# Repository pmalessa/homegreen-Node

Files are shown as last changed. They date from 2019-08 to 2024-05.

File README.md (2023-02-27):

# HomeGreen - self watering system
## Description
A self watering system for outdoor plants. This project contains the hardware and software files to completely build a HomeGreen node on your own.

The system is based on an inexpensive node, which is able to control up to 3 pumps and can be powered by nearly any conventional powerbank. It has a basic user interface using a 6-Digit 7-Segment Display combined with 4 touch buttons. As a pump, you could either use a 4-6V DC pump or a 5V relay to control a higher voltage pump. The node is designed to be water resistant and can be easily mounted using embedded magnets or a 3D printed holder.

## Repository structure
This repo contains everything you need to build a homegreen node on your own:

- hardware: The EAGLE PCB and GERBER files, BOM and models and dimensions for the case
- firmware: The firmware for the microcontroller (attiny88) on the node

## Hardware
The HomeGreen node PCB is designed to be enclosed in a 25mm diameter transparent pipe to be water resistant. The touch buttons can be used through the pipe without the need to open the case. The 2 ends need plastic caps, which could be easily 3D printed. one needs to be fully closed, while the other one needs to have an opening the for USB-A connector of the pump as well as the micro USB connector of the powerbank.

## Firmware
The firmware is written in low-level C++ and uses the PlatformIO framework. It is designed to run as energy efficient as possible to be able to run on a powerbank for a long time.

## Detailed description
The HomeGreen node contains the following main components:
- an attiny88 microcontroller as main controller
- a sophisticated power management circuit to be able to sleep and wake up the connected powerbank regularly
- a 6-Digit 7-Segment Display with its controller as user interface
- a 4-Channel touch button controller as user interface
- an I2C temperature sensor to measure the temperature of the environment
- a current limiter, step-up converter and a current measurement circuit to adjust and monitor the output power for the pump
- the ability to control up to 3 pumps sequentially using an additional HomeGreen Pump Hub

### Power management
The main issue of supplying your gadgets using a powerbank is the fact, that nearly all powerbanks shut off after a certain time of inactivity. As the sleep current draw of the HomeGreen node is substantially lower than any charge current the powerbank is designed for, it treats it as inactive and shuts off eventually. 

This led to the necessity to have a supercapacitor as an additional short-time energy storage onboard to be able to power the controller while in sleep and only wake the powerbank once the supercap is drained or it is time to enable the pump.

Additionally, each powerbank is behaving differently when it comes to the sleep and wake behavior. Some powerbanks wake up immediately once you connect the capacitive load of the supercap, while others require an additional substantial resistive load to enable its regulators. Strangely, some powerbanks even change their polarity and apply -2.5V to their output!

To support most of the available powerbanks on the market 2 MOSFETS back to back, combined with a charge pump and an additional controllable resistive load was necessary. Even with that, some powerbanks do not work reliably and should be avoided. A list of tested powerbanks will be added.

### User Interface
The HomeGreen Node consists of a 6-Digit 7-Segment display as well as 4 touch buttons to view its status and adjust all parameters to your needs. The HomeGreen Node can be used to control up to 3 pumps using an additional HomeGreen Pump Hub. Once connected, the user interface switches to the ability to adjust timing of each pump separately. However, if no Pump Hub is connected, it is simplyfied to control just one pump.

#### Sleep State
In its default sleep state, the 7-Segment Display is turned off and only the 2 Status LEDs are displaying its state. 
- If it blinks green once every 8 seconds, everything is fine. 
- If it blinks green twice and in a faster interval, it charges its supercap. This happens every 5-15mins. 
- If it blinks red, an error occured and the Node should be checked by waking it to get more details.
- If it is time to water the plants, it will wake itself and continue with the Pump State.
- To wake the Node, just touch one of its touch buttons. It will then try to wake the powerbank and will turn on its Display, once successful. It may take multiple tries sometimes depending on the model of powerbank. It then moves into Info State. If an error occured, it will switch into Error State after wake up before going to Info State.

#### Info State
In the info state, you see the set interval and duration of the pump cycle as well as the time left till the next pump cycle at one glance. If a Pump Hub is connected, you can switch between the config for each pump with a short press of the SET button.
- If no button is pressed, it shuts off and switches back to Sleep State after some time.
- To adjust the interval or duration of the pump cycle, long press the SET button and wait for the display to fade out and in. It now switched into Config State.
- To start a manual pump cycle, just long press the MANUAL button. It then switches into Pump State.

#### Config State
In the Config State, you can adjust the interval and duration of the pump cycle. The currently selected parameter is displayed by blinking its number.
- To increase the parameter, short press or hold the + button.
- To decrease the parameter, short press of hold the - button.
- To switch the selected parameter, short press the SET button.
- To save the newly configured parameters, long press the SET button. It switches to Info State then.
- If no button have been pressed for a longer period, changes are discarded and it switches to Info State.
- To get more advanced information and configuration options, long press the MANUAL button to switch to Advanced State.

#### Pump State
Once the pump interval elapsed or a manual pump cycle has been started, the Node switches into Pump State. In Pump State, an animation is displayed as well as the time left to pump in the current cycle. If a Pump Hub is connected, it will additionally display which pump is currently enabled.
- To increase the current pump cycle by 1 minute, short press the + button.
- To decrease the current pump cycle by 1 minute, short press the - button.
- To manually switch to the next pump, short press the SET button.
- To stop the current pump cycle, long press the MANUAL button.
- Once the pump duration of all pumps elapsed, the Node will switch to Info State to shortly display its current parameters, and after some time of inactivity it switches back to Sleep State.

#### Error State
If an error ocurred, the red led blinks to signal that something went wrong. To check for details, wake the node and it will switch to this state.
The following errors are possible:
- PB_ERR: Powerbank-Error - The node was not possible to wake the powerbank at its last wake up by a pump cycle or a user action. Check the charge state or cabling of the powerbank. Maybe that model is incompatible with the Node, check the list of tested powerbanks for hints.
- P1_ERR/P2_ERR/P3_ERR: Pump1/2/3-Error - There is an issue with the mentioned pump, the current draw had an anomaly. Maybe the cable is broken, the water tank is empty or the pump is clogged.
- EP_ERR: EEPROM-Error - There is an issue with the save state of the configuration. This rarely happens, but sometimes the config can get corrupted by battery drain. The config will be reset to default state and it has to be reconfigured.

The following interactions are possible:
- To clear the current error, short press any button.
- To ignore the current error permanently (until the next reset to defaults), long press the MANUAL button.

#### Advanced State
The Advanced State contains additional information and configuration options to move through.
The following informations are displayed:
- The build date of the firmware
- The build version of the firmware
- The current runtime in hours
- The total runtime in hours

The following interactions are possible:
- To move to the next information, short press the SET button
- To leave the Advanced State back to Info State, long press the SET button
- To reset all configurations to its default state, long press the MANUAL button. It then switches back to Info State.

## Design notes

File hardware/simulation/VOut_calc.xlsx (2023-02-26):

R1 [Ohm] | 91000.00
R2 [Ohm] | 10000.00
R3 [Ohm] | 100000.00
R4 [Ohm] | 100000.00
C1 [F]
VREF [V] | 0.60
V_PWM_H [V] | 3.30
V_PWM_L [V] | 0.00
VOUT_CONST | 6.06
Duty Cycle [%] | 0 | 10 | 20 | 30 | 40 | 50 | 60 | 70 | 80 | 90 | 100
PWM Voltage | 0.00 | 0.33 | 0.66 | 0.99 | 1.32 | 1.65 | 1.98 | 2.31 | 2.64 | 2.97 | 3.30
VOUT | 6.33 | 6.18 | 6.03 | 5.88 | 5.73 | 5.58 | 5.43 | 5.28 | 5.13 | 4.98 | 4.83

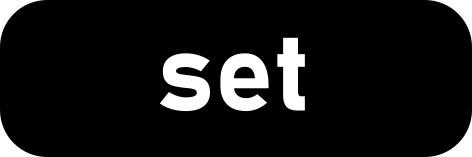
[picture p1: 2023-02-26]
design_files/bitmaps/button_set.png

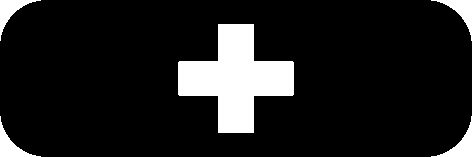
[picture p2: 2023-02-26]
design_files/bitmaps/button_plus.bmp

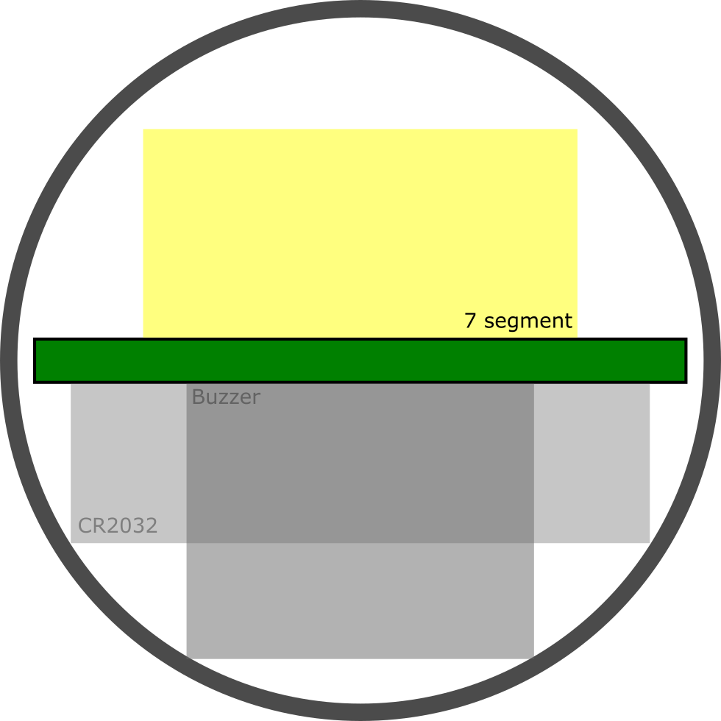
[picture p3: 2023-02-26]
design_files/svgs/Pipe.png

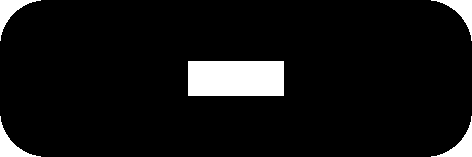
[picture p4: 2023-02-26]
design_files/bitmaps/button_minus.bmp

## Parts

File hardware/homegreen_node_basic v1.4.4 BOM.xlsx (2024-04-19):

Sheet: Sheet1
Qty | Value | Device | Package | Parts | Description
1 |  | ATTINY88 | TQFP32-08 | IC1
1 | 61400416021 | 61400416021 | 61400416021 | X3.1 | WR-COM USB 2.0 Type A Horizontal
1 | 0.33F | SUPERCAP | C_FYD0H104ZF | C3.1
10 | 100k | R-EU_R0805 | R0805 | R5.1, R5.2, R5.3, R5.4, R5.5, R5.6, R5.7, R5.8, R5.9, R5.10 | RESISTOR, European symbol
8 | 100n | C-EUC0805 | C0805 | C1.1, C1.2, C1.3, C1.4, C1.5, C1.6, C1.7, C1.8 | CAPACITOR, European symbol
3 | 10k | R-EU_R0805 | R0805 | R1.1, R1.2, R1.3 | RESISTOR, European symbol
4 | 10u | C-EUC0805 | C0805 | C2.1, C2.2, C2.3, C2.4 | CAPACITOR, European symbol
1 | 1M | R-EU_R0805 | R0805 | R6.1 | RESISTOR, European symbol
6 | 1k | R-EU_R0805 | R0805 | R2.1, R2.2, R2.3, R2.4, R2.5, R2.6 | RESISTOR, European symbol
1 | 20m | R-EU_R0805 | R0805 | R8.1 | RESISTOR, European symbol
1 | 330u | CPOL-EUD | PANASONIC_D | C4.1 | POLARIZED CAPACITOR, European symbol
2 | 3k | R-EU_R0805 | R0805 | R4.1, R4.2 | RESISTOR, European symbol
2 | 47 | R-EU_R0805 | R0805 | R3.1, R3.2 | RESISTOR, European symbol
3 | 4k7 | R-EU_R0805 | R0805 | R7.1, R7.2, R7.3 | RESISTOR, European symbol
4 | 5p | C-EUC0805 | C0805 | C5.1, C5.2, C5.3, C5.4 | CAPACITOR, European symbol
1 | 7-SEGMENT-6DIGIT-FJ3661BH | 7-SEGMENT-6DIGIT-FJ3661BH | 7SEG_6D_FJ3661BH | SEG1.1 | 2 Digit 7 Segment Display
3 | BAT54S | BAT54S | SOT23 | D1.1, D1.2, D1.3 | Schottky Diodes
2 | BC817DPN | BC817DPN | SOT23-6 | Q2.1, Q2.2
1 | DHT-4235A | SMD-BUTTON-TOP-DHT-4235A(4P-4.2X3.2MM) | SW4-SMD-4.2X3.2X2.5MM | SW1.1 | 311020045
1 | DSS24 | DIODE_SOD123 | SOD-123 | D2.1
1 | INA180 | INA180 | SOT23-5 | IC5.1
1 | JST-XH-06-PIN-ANGLED | JST-XH-06-PIN-ANGLED | JST-XH-06-PACKAGE-ROUND-PAD-ANGLED | X1.1 | JST XH Connector 2 Pin
1 | LM75B | LM75B | SO8 | IC2.1 | Digital temperature sensor and thermal watchdog
1 | MT3608 | MT3608 | SOT23-6 | IC8.1
1 | MT9700MT9700 | MT9700MT9700 | SOT23-5 | IC4.1
1 | TM1637-sop20 | DRIVER-TM1637(SOP20) | SOP20-1.27-12.7X7.65MM | IC6.1 | 310040027
1 | TTP224NS | TTP224NS | SSOP16 | IC3.1
1 | TYA40202R2M-10 | WE-LQSH_4020_744050420047 | WE-LQSH_4020 | L1.1 | WE-LQSH SMD Semi-Shielded High Saturation Power Inductor
1 | WST2011 | CJL2623SOT23-6 | SOT23-6 | Q1.1
1 | ZX62-B-5PA | MICRO-USB-SMD(ZX62-B-5PA) | ZX62-B-5PA | X2.1 | 320010005
1 | green | LEDKA-3528ASYC | KA-3528ASYC | LED1.1 | LED
1 | red | LEDKA-3528ASYC | KA-3528ASYC | LED2.1 | LED
2 | white | LEDCHIPLED_0805 | CHIPLED_0805 | LED3.1, LED3.2 | LED

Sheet: BOM
Qty | Value | Device | Package | Side | LCSC MPN | MPN | Link | Parts | needed for 30 pcbs | in stock | order lcsc
1 |  | ATTINY88 | TQFP32-08 | top | C111451 | ATTINY88-AU | https://lcsc.com/product-detail/ATMEL-AVR_MICROCHIP_ATTINY88-AU_ATTINY88-AU_C111451.html | IC1 | 30
1 | 61400416021 | 61400416021 | 61400416021 | top | C42643 | C42643 | https://lcsc.com/product-detail/USB-Connectors_Jing-Extension-of-the-Electronic-Co-C42643_C42643.html | X3.1 | 30
1 | 0.33F | SUPERCAP | C_FYD0H104ZF | bot | - |  |  | C3.1 | 30
10 | 100k | R-EU_R0805 | R0805 | 1xtop+9xbot | C96346 | RC0805FR-07100KL | https://lcsc.com/product-detail/Chip-Resistor-Surface-Mount_YAGEO-RC0805FR-07100KL_C96346.html | R5.1, R5.2, R5.3, R5.4, R5.5, R5.6, R5.7, R5.8, R5.9, R5.10 | 300
8 | 100n | C-EUC0805 | C0805 | bot | C49678 | CC0805KRX7R9BB104 | https://lcsc.com/product-detail/Multilayer-Ceramic-Capacitors-MLCC-SMD-SMT_YAGEO-CC0805KRX7R9BB104_C49678.html | C1.1, C1.2, C1.3, C1.4, C1.5, C1.6, C1.7, C1.8 | 240
3 | 10k | R-EU_R0805 | R0805 | bot |  |  |  | R1.1, R1.2, R1.3 | 90
4 | 10u | C-EUC0805 | C0805 | bot | C91245 | CL21A106MPFNNNE | https://lcsc.com/product-detail/Multilayer-Ceramic-Capacitors-MLCC-SMD-SMT_Samsung-Electro-Mechanics-CL21A106MPFNNNE_C91245.html | C2.1, C2.2, C2.3, C2.4 | 120
1 | 1M | R-EU_R0805 | R0805 | bot | C107699 | RC0805JR-071ML | https://lcsc.com/product-detail/Chip-Resistor-Surface-Mount_YAGEO-RC0805JR-071ML_C107699.html | R6.1 | 30
6 | 1k | R-EU_R0805 | R0805 | 2xtop+4xbot | C100046 | RC0805JR-071KL | https://lcsc.com/product-detail/Chip-Resistor-Surface-Mount_YAGEO-RC0805JR-071KL_C100046.html | R2.1, R2.2, R2.3, R2.4, R2.5, R2.6 | 180
1 | 20m | R-EU_R0805 | R0805 | 0 Ohm R? | C728492 | RL0805JR-070R02L | https://lcsc.com/product-detail/Chip-Resistor-Surface-Mount_YAGEO-RL0805JR-070R02L_C728492.html | R8.1 | 30 |  | 100
1 | 330u | CPOL-EUD | PANASONIC_D | bot | C128454 | EEEFTC331XAP | https://lcsc.com/product-detail/Aluminum-Electrolytic-Capacitors-SMD_PANASONIC-EEEFK0J331XP_C128454.html | C4.1 | 30
2 | 3k | R-EU_R0805 | R0805 | bot | C126350 | RC0805FR-073KL | https://lcsc.com/product-detail/Chip-Resistor-Surface-Mount_3KR-3001-1_C126350.html | R4.1, R4.2 | 60
2 | 47 | R-EU_R0805 | R0805 | 1xtop+1xbot | C107118 | CC0805JRNPO9BN470 | https://lcsc.com/product-detail/Multilayer-Ceramic-Capacitors-MLCC-SMD-SMT_YAGEO-CC0805JRNPO9BN470_C107118.html | R3.1, R3.2 | 60
3 | 4k7 | R-EU_R0805 | R0805 | bot | C60816 | RC0805FR-074K7L | https://lcsc.com/product-detail/Chip-Resistor-Surface-Mount_4-7K-4701-1_C60816.html | R7.1, R7.2, R7.3 | 90 |  | 200
4 | 5p | C-EUC0805 | C0805 | bot | C513573 | CL21C050CBANNNC | https://lcsc.com/product-detail/Multilayer-Ceramic-Capacitors-MLCC-SMD-SMT_YAGEO-CC0805DRNPO9BN5R0_C513573.html | C5.1, C5.2, C5.3, C5.4 | 120
1 | 7-SEGMENT-6DIGIT-FJ3661BH | 7-SEGMENT-6DIGIT-FJ3661BH | 7SEG_6D_FJ3661BH | top | C68298 | FJ3661BH | https://lcsc.com/product-detail/Led-Segment-Display_Shenzhen-Zhihao-Elec-FJ3661BH_C68298.html | SEG1.1 | 30
3 | BAT54S | BAT54S | SOT23 | top 9pcbs | C181201 | BAT54S | https://lcsc.com/product-detail/Schottky-Barrier-Diodes-SBD_Guangdong-Hottech-BAT54S_C181201.html | D1.1, D1.2, D1.3 | 90
2 | BC817DPN | BC817DPN | SOT23-6 | top 0 | C426778 | BC817DPN,115 | https://lcsc.com/product-detail/New-Arrivals_Nexperia-BC817DPN-115_C426778.html | Q2.1, Q2.2 | 60
1 | DHT-4235A | SMD-BUTTON-TOP-DHT-4235A(4P-4.2X3.2MM) | SW4-SMD-4.2X3.2X2.5MM | bot | C92589 | K2-1808SN-A4SW-01 | https://lcsc.com/product-detail/Tactile-Switches_Korean-Hroparts-Elec-K2-1808SN-A4SW-01_C92589.html | SW1.1 | 30
1 | DSS24 | DIODE_SOD123 | SOD-123 | top | C511865 | DSS24 | https://lcsc.com/product-detail/Schottky-Barrier-Diodes-SBD_BORN-DSS24_C511865.html | D2.1 | 30 |  | 40
1 | INA180A2 | INA180 | SOT23-5 | top | C192764 | INA180A2IDBVR | https://lcsc.com/product-detail/Operational-Amplifiers_Texas-Instruments-Texas-Instruments-INA180A2IDBVR_C192764.html | IC5.1 | 30 |  | 40
1 | JST-XH-06-PIN-ANGLED | JST-XH-06-PIN-ANGLED | JST-XH-06-PACKAGE-ROUND-PAD-ANGLED | bot | - | - | - | X1.1 | 30
1 | LM75B | LM75B | SO8 | bot | C34565 | LM75BD,118 | https://lcsc.com/product-detail/Temperature-Sensors_NXP-Semicon-LM75BD-118_C34565.html | IC2.1 | 30
1 | MT3608 | MT3608 | SOT23-6 | top | C84817 | MT3608 | https://lcsc.com/product-detail/DC-DC-Converters_XI-AN-Aerosemi-Tech-MT3608_C84817.html | IC8.1 | 30 |  | 50
1 | MT9700MT9700 | MT9700MT9700 | SOT23-5 | top | C89855 | MT9700 | https://lcsc.com/product-detail/PMIC-Power-Distribution-Switches_MT9700_C89855.html | IC4.1 | 30
1 | TM1637-sop20 | DRIVER-TM1637(SOP20) | SOP20-1.27-12.7X7.65MM | top | C265472 | TM1637 | https://lcsc.com/product-detail/LED-Drivers_GN-Semic-GN1637_C265472.html | IC6.1 | 30
1 | TTP224NS | TTP224NS | SSOP16 | top | C94149 | TTP224B-BSBN | https://lcsc.com/product-detail/Touch-Screen-Controller-ICs_Tontek-Design-Tech-TTP224B-BSBN_C94149.html | IC3.1 | 30
1 | TYA40202R2M-10 | WE-LQSH_4020_744050420047 | WE-LQSH_4020 | top 10 pcbs | C326299 | SNR4018K-2R2M | https://lcsc.com/product-detail/Power-Inductors_3L-COILS-SNR4018K-2R2M_C326299.html | L1.1 | 30 |  | 33
1 | WST2011 | CJL2623SOT23-6 | SOT23-6 | top | C148368 | WST2011 | https://lcsc.com/product-detail/MOSFET_Winsok-Semicon-WST2011_C148368.html | Q1.1 | 30
1 | ZX62-B-5PA | MICRO-USB-SMD(ZX62-B-5PA) | ZX62-B-5PA | bot | C10418 | C10418 | https://lcsc.com/product-detail/USB-Connectors_Jing-Extension-of-the-Electronic-Co-C10418_C10418.html | X2.1 | 30
1 | green | LEDKA-3528ASYC | KA-3528ASYC | top | C440443 | TJ-S3528UG6W9TLC2G-A5 | https://lcsc.com/product-detail/Light-Emitting-Diodes-LED_TOGIALED-TJ-S3528UG6W9TLC2G-A5_C440443.html | LED1.1 | 30
1 | red | LEDKA-3528ASYC | KA-3528ASYC | top | C74350 | 67-21/R6C-FN2Q1BZ/2T | https://lcsc.com/product-detail/Light-Emitting-Diodes-LED_Everlight-Elec-67-21-R6C-FN2Q1BZ-2T_C74350.html | LED2.1 | 30
2 | white | LEDCHIPLED_0805 | CHIPLED_0805 | top | C84258 | NCD0805W2 | https://lcsc.com/product-detail/Light-Emitting-Diodes-LED_Foshan-NationStar-Optoelectronics-NCD0805W2_C84258.html | LED3.1, LED3.2 | 60

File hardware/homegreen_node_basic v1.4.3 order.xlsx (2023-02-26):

Qty | Value | Device | Package | LCSC MPN | MPN | needed for 30 pcbs | in machine | in stock | order lcsc | order mouser | order reichelt | order ali
2 |  | 61400416021 | 61400416021 | C42643 | C42643 | 60 | - | 170
1 |  | ATTINY88 | TQFP32-08 | C111451 | ATTINY88-AU | 30 | - | 15 |  | 30
1 | 0.33F | SUPERCAP | C_FYD0H104ZF | - | - | 30 | - | 41
10 | 100k | R-EU_R0805 | R0805 | C96346 | RC0805FR-07100KL | 300 | 500
13 | 100n | C-EUC0805 | C0805 | C49678 | CC0805KRX7R9BB104 | 390 | 500
9 | 10u | C-EUC0805 | C0805 | C91245 | CL21A106MPFNNNE | 270 | 0 | 100 | 100
4 | 1M | R-EU_R0805 | R0805 | C107699 | RC0805JR-071ML | 120 | 500
14 | 1k | R-EU_R0805 | R0805 | C100046 | RC0805JR-071KL | 420 | 100 | 400
2 | 330u | CPOL-EUD | PANASONIC_D | C128454 | EEEFTC331XAP | 60 | - | 60
2 | 3k | R-EU_R0805 | R0805 | C126350 | RC0805FR-073KL | 60 | 150
3 | 47 | R-EU_R0805 | R0805 | C107118 | CC0805JRNPO9BN470 | 90 | 200
8 | 5p | C-EUC0805 | C0805 | C513573 | CL21C050CBANNNC | 240 | 200
4 | 6k8 | R-EU_R0805 | R0805 | C114550 | RC0805FR-076K8L | 120 | 200
2 | 7-SEGMENT-6DIGIT-FJ3661BH | 7-SEGMENT-6DIGIT-FJ3661BH | 7SEG_6D_FJ3661BH | C68298 | FJ3661BH | 60 | - | 6 | 35
2 | 74AHC1G66 | 74AHC1G66 | SOT65P212X110-5N | C96224 | 74AHC1G66GW,125 | 60 | 0 | 0 | 100
5 | BAT54S | BAT54S | SOT23 | C181201 | BAT54S | 150 | 200 |  | 0
4 | BC817DPN | BC817DPN | SOT23-6 | C426778 | BC817DPN,115 | 120 | 0 | 0 | 150
2 | WST2011 | CJL2623SOT23-6 | SOT23-6 | C148368 | WST2011 | 60 | 0 | 80 | 50
2 | DHT-4235A | SMD-BUTTON-TOP-DHT-4235A(4P-4.2X3.2MM) | SW4-SMD-4.2X3.2X2.5MM | C92589 | K2-1808SN-A4SW-01 | 60 | - | 24 | 100
1 | LM75B | LM75B | SO8 | C34565 | LM75BD,118 | 30 | 0 | 5 | 40
2 | MT9700MT9700 | MT9700MT9700 | SOT23-5 | C89855 | MT9700 | 60 | 0 | 35 | 100
2 | TM1637-sop20 | DRIVER-TM1637(SOP20) | SOP20-1.27-12.7X7.65MM | C265472 | TM1637 | 60 | - | 7 | 100
2 | TTP224NS | TTP224NS | SSOP16 | C94149 | TTP224B-BSBN | 60 | - | 8 |  |  |  | 100
2 | ZX62-B-5PA | MICRO-USB-SMD(ZX62-B-5PA) | ZX62-B-5PA | C10418 | C10418 | 60 | - | 100+ | 0
2 | green | LEDKA-3528ASYC | KA-3528ASYC | C440443 | TJ-S3528UG6W9TLC2G-A5 | 60 | 0 | 0 | 100
2 | red | LEDKA-3528ASYC | KA-3528ASYC | C74350 | 67-21/R6C-FN2Q1BZ/2T | 60 | 0 | 0 | 100
4 | white | LEDCHIPLED_0805 | CHIPLED_0805 | C84258 | NCD0805W2 | 120 | 0 | 0 | 200
1 | JST-XH-06-PIN-ROUND-PAD | JST-XH-06-PIN-ROUND-PAD | JST-XH-06-PACKAGE-ROUND-PAD | - | - | 30 | - |  |  |  | 50
1 |  | CONN_02JST-PTH-2 | JST-2-PTH | - |  | 5 | 0 | 0 |  |  | 10
1 |  | CONN_04JST-PTH | JST-4-PTH | - |  | 5 | 0 | 0 |  |  | 10
2 | 12p | C-EUC0805 | C0805 | C107108 | CC0805JRNPO9BN120 | 10 | 0 | 0 | 100
1 | 2k4 | R-EU_R0805 | R0805 | C114521 | RC0805FR-072K4L | 5 | 0 | 0 | 100
1 | 32.768kHz | CRYSTAL-32.768KHZSMD-3.2X1.5 | CRYSTAL-SMD-3.2X1.5MM | C48615 | Q13FC1350000200 | 5 | 0 | 0 | 10
2 | 74AHCT1G125 | 74AHCT1G125 | SOT353 | C12495 | 74AHCT1G125GW,125 | 10 | 0 | 0 | 20
1 | 7k5 | R-EU_R0805 | R0805 | C114547 | RC0805FR-077K5L | 5 | 0 | 0 | 100
1 | DMP3098 | PMOSSOT23 | SOT23-3 | C150492 | DMP3098L-7 | 5 | 0 | 0 | 20
2 | DSS24 | DIODE_SOD123 | SOD-123 | C466482 | DSS24 | 10 | 0 | 0 | 20
1 | DW06D | DW06D | SOT23-6 | C82123 | DW06D | 5 | 0 | 0 | 10
1 | ME6209A33M3G | ME6209SOT23-3 | SOT23-3 | C83508 | ME6209A33M3G | 5 | 0 | 0 | 10
1 | MT3608 | MT3608 | SOT23-6 | C84817 | MT3608 | 5 | 0 | 0 | 10
1 | TMP236 | TMP236 | SOT353 | C496107 | TMP236A4DCKR | 5 | 0 | 0 | 10
1 | TP4056 | TP4056 | ESOP-8 | C725790 | TP4056 | 5 | 0 | 0 | 10
1 | TYA40202R2M-10 | WE-LQSH_4020_744050420047 | WE-LQSH_4020 | C326299 | SNR4018K-2R2M | 5 | 0 | 0 | 10
1 | UBLOX_BMD_3XX | UBLOX_BMD_3XX | UBLOX_BMD_3XX | Mouser | BMD-360-A-R | 5 | 0 | 0 |  | 5

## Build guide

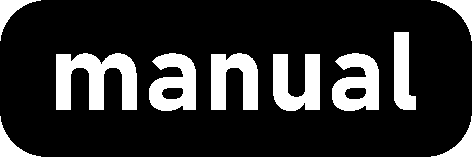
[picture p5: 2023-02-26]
design_files/bitmaps/button_manual.bmp

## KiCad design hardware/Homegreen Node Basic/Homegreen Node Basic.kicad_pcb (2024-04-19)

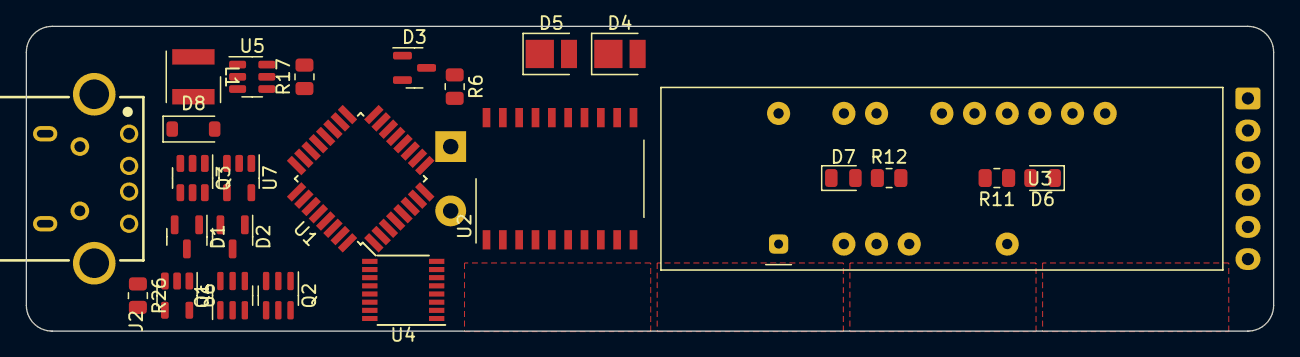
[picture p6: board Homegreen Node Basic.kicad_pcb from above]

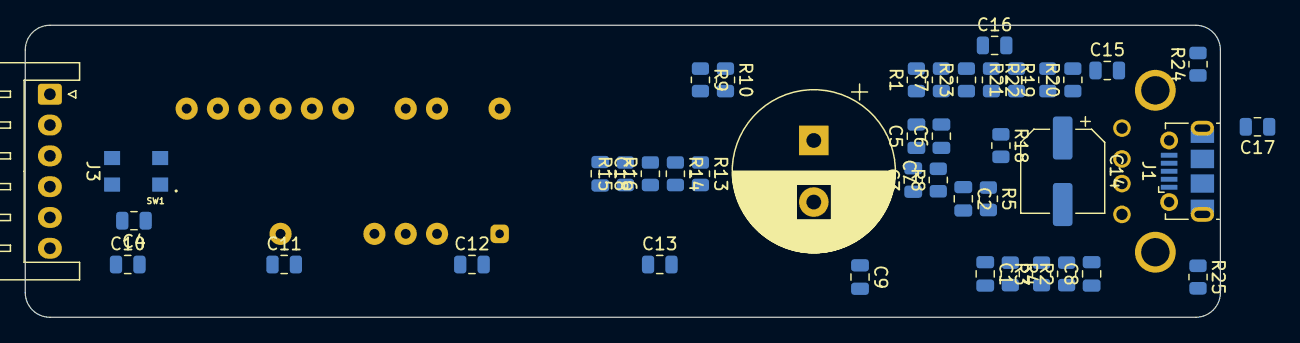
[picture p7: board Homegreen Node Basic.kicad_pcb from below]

Board: 2 copper layers, 97.0 x 23.7 mm, 67 parts (42 on the bottom side), 63 nets, no tracks yet.

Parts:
C1, C2, C3, C4, C5, C6, C8, C9, C18: 100n; C_0805_2012Metric
C7: 0.33F; CP_Radial_D13.0mm_P5.00mm
C10, C11, C12, C13: 5p; C_0805_2012Metric
C14: 330u; CP_Elec_6.3x5.8
C15, C16, C17: 10u; C_0805_2012Metric
D1, D2, D3: BAT54S; SOT-23
D4: gr; LED_PLCC_2835
D5: red; LED_PLCC_2835
D6, D7: wh; LED_0805_2012Metric
D8: DSS24; D_SOD-123
J1: USB_B_Micro; USB_Micro-B_Molex-105017-0001
J2: USB_A; Wuerth_61400416021
J3: Conn_01x06_Pin; JST_XH_S6B-XH-A_1x06_P2.50mm_Horizontal
L1: 2.2u; L_Wurth_WE-LQSH-4020
Q1, Q2: BC817DPN; SC-74-6_1.5x2.9mm_P0.95mm
Q3: WST2011; SOT-23-6
R1, R3, R7, R8, R15, R16, R17, R20, R24, R25: 100k; R_0805_2012Metric
R2, R6: 47; R_0805_2012Metric
R4, R11, R12, R13, R14, R21: 1k; R_0805_2012Metric
R5: 1M; R_0805_2012Metric
R9, R10: 3k; R_0805_2012Metric
R18: 4k7; R_0805_2012Metric
R19, R22, R23: 10k; R_0805_2012Metric
R26: 20m; R_0805_2012Metric
SW1: SW_Push; SW_DHT-4235A
U1: ATtiny88-A; TQFP-32_7x7mm_P0.8mm
U2: TM1637; SO-20_12.8x7.5mm_P1.27mm
U3: FJ3661BH
U4: TTP224; SSOP-16_3.9x4.9mm_P0.635mm
U5: MT3608; SOT-23-6
U6: INA180A2; SOT-23-5
U7: MT9700; SOT-23-5

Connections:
/BTN_LED: R11.2, R12.2, U1.8 (PB7)
/EN_CLK: C1.2, U1.13 (PB1)
/EN_LOAD: Q1.2 (B1), R4.2, U1.30 (PD0)
/EN_PUMP: R17.1, U1.22 (PA1), U5.4 (EN), U7.4 (EN)
/LED_ERR: R10.2, U1.11 (PD7)
/LED_OK: R9.2, U1.14 (PB2)
/MISO: J3.1, U1.16 (PB4)
/MOSI: J3.4, U1.15 (PB3)
/PUMP_CURRENT: U1.26 (PC3), U6.1
/PUMP_VOL: R23.1, U1.23 (PC0)
/RESET: C3.2, C4.1, J3.5, R8.1, SW1.1, U1.29 (~RESET/PC6)
/SCK: J3.3, U1.17 (PB5)
/TM_CLK: R13.2, R15.1, U1.10 (PD6)
/TM_DIO: R14.2, R16.1, U1.9 (PD5)
/TOUCH_PWR: C9.1, U1.3 (PA2), U4.6 (VDD), U4.11 (OD)
/USB1: J2.2 (D-), R24.1, U1.24 (PC1)
/USB2: J2.3 (D+), R25.1, U1.12 (PB0)
/User Interface/DIG1: U2.15 (GRID1), U3.22 (CA1)
/User Interface/DIG2: U2.14 (GRID2), U3.3 (CA2)
/User Interface/DIG3: U2.13 (GRID3), U3.4 (CA3)
/User Interface/DIG4: U2.12 (GRID4), U3.16 (CA4)
/User Interface/DIG5: U2.11 (GRID5), U3.13 (CA5)
/User Interface/DIG6: U2.10 (GRID6), U3.12 (CA6)
/User Interface/PAD_MANUAL: C13.1, U4.4 (TP3)
/User Interface/PAD_MINUS: C12.1, U4.3 (TP2)
/User Interface/PAD_PLUS: C10.1, U4.1 (TP0)
/User Interface/PAD_SET: C11.1, U4.2 (TP1)
/~EN_PB: D2.1 (A), U1.25 (PC2)
BAT_PWR: C3.1, C5.1, C6.1, C7.1, J3.2, R6.2, R8.2, U1.4 (VCC), U1.18 (AVCC)
GND: C2.2, C4.2, C5.2, C6.2, C7.2, C8.2, C9.2, C10.2, C11.2, C12.2, C13.2, C14.2, C15.2, C16.2, C17.2, C18.2, D4.1 (K), D5.1 (K), D6.1 (K), D7.1 (K), J1.5 (GND), J1.6 (Shield), J2.5 (Shield), J3.6, R2.2, R5.2, R7.1, R17.2, R18.2, R21.2, R24.2, R25.2, R26.2, SW1.2, U1.5 (GND), U1.21 (GND), U2.1 (GND), U4.5 (AHLB), U4.8 (LPMB), U4.10 (VSS), U5.2 (GND), U6.2 (GND), U6.4 (-), U7.2 (GND)
unnamed: C16.1, R22.1, R23.2
unnamed: D1.1 (A), Q2.1 (E1), R3.1
unnamed: D1.3 (COM), J1.1 (VBUS), Q3.6 (D)
unnamed: D1.2 (K), Q1.5 (B2), Q1.6 (C1)
unnamed: C1.1, D2.3 (COM)
unnamed: C2.1, D2.2 (K), Q3.1 (G), Q3.3 (G), R5.1
unnamed: D3.3 (COM), R6.1
unnamed: D4.2 (A), R9.1
unnamed: D5.2 (A), R10.1
unnamed: D6.2 (A), R11.1
unnamed: D7.2 (A), R12.1
unnamed: D8.2 (A), L1.2, U5.1 (SW)
unnamed: C14.1, C17.1, D8.1 (K), J2.1 (VBUS), R19.1, R20.1
unnamed: J2.4 (GND), R26.1, U6.3 (+)
unnamed: Q1.1 (E1), Q2.6 (C1), R2.1
unnamed: Q1.3 (C2), Q2.2 (B1), R3.2
unnamed: Q1.4 (E2), R4.1
unnamed: Q3.2 (S), Q3.5 (S)
unnamed: R1.1, R7.2, U1.19 (PA0)
unnamed: R13.1, U2.18 (CLK)
unnamed: R14.1, U2.17 (DIO)
unnamed: U2.2 (SEG1/KS1), U3.15 (A)
unnamed: U2.3 (SEG2/KS2), U3.20 (B)
unnamed: U2.4 (SEG3/KS3), U3.19 (C)
unnamed: U2.5 (SEG4/KS4), U3.5 (D)
unnamed: U2.6 (SEG5/KS5), U3.1 (E)
unnamed: U2.7 (SEG6/KS6), U3.14 (F)
unnamed: U2.8 (SEG7/KS7), U3.17 (G)
unnamed: U2.9 (SEG8/KS8), U3.8 (DP)
unnamed: R19.2, R20.2, R21.1, R22.2, U5.3 (FB)
unnamed: C15.1, L1.1, U5.5 (IN), U7.1 (VOUT)
unnamed: R18.1, U7.3 (SET)
USB_PWR: C8.1, C18.1, D3.1 (A), Q3.4 (D), R1.2, R15.2, R16.2, U2.16 (VDD), U6.5 (V+), U7.5 (VIN)

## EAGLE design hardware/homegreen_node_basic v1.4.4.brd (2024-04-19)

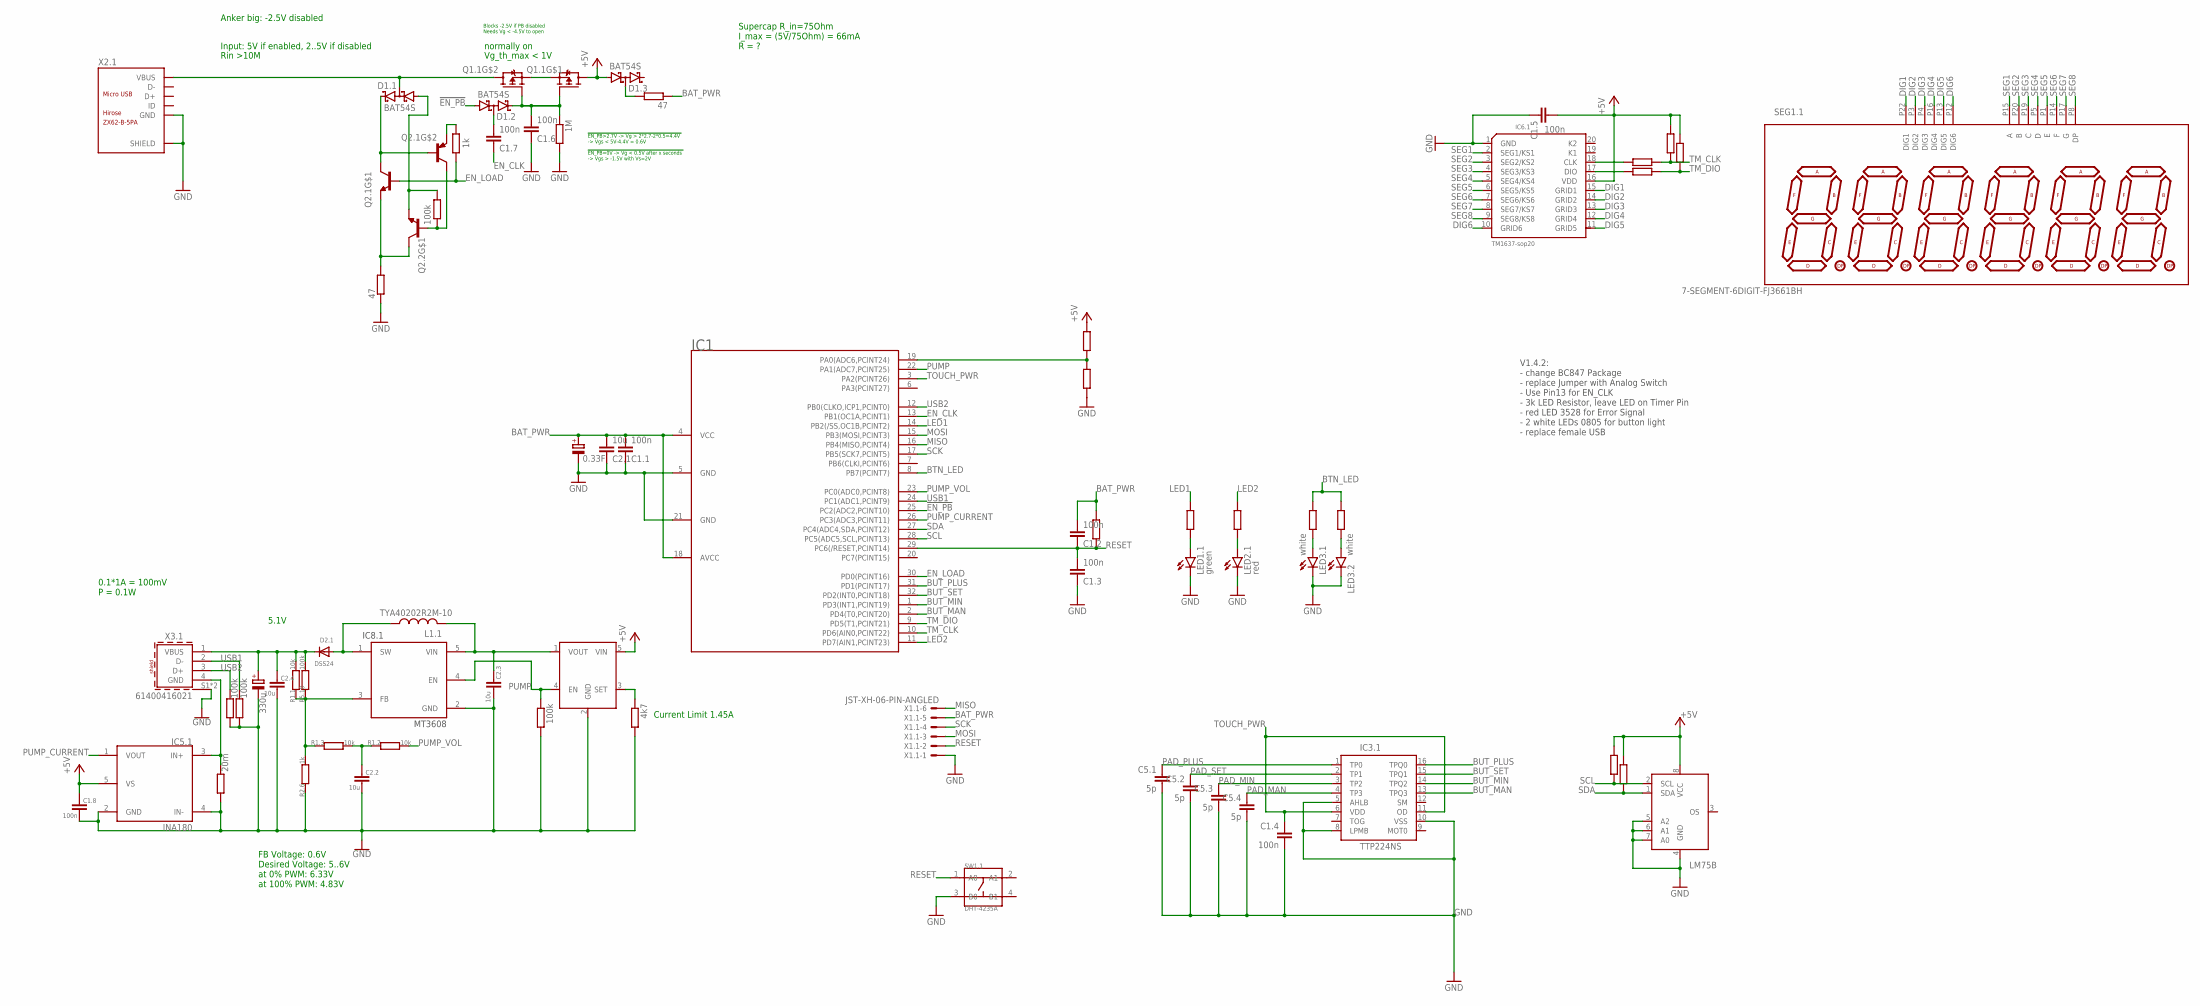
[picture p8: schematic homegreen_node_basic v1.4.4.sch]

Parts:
C1.1, C1.2, C1.3, C1.4, C1.5, C1.6, C1.7, C1.8: 100n; C0805
C2.1, C2.2, C2.3, C2.4: 10u; C0805
C3.1: 0.33F; C_FYD0H104ZF
C4.1: 330u; PANASONIC_D
C5.1, C5.2, C5.3, C5.4: 5p; C0805
D1.1, D1.2, D1.3: BAT54S; SOT23
D2.1: DSS24; SOD-123
IC1: ATTINY88; TQFP32-08
IC2.1: LM75B; SO8
IC3.1: TTP224NS; SSOP16
IC4.1: MT9700MT9700; SOT23-5
IC5.1: INA180; SOT23-5
IC6.1: TM1637-sop20; SOP20-1.27-12.7X7.65MM
IC8.1: MT3608; SOT23-6
L1.1: TYA40202R2M-10; WE-LQSH_4020
LED1.1: green; KA-3528ASYC
LED2.1: red; KA-3528ASYC
LED3.1, LED3.2: white; CHIPLED_0805
Q1.1: WST2011; SOT23-6
Q2.1, Q2.2: BC817DPN; SOT23-6
R1.1, R1.2, R1.3: 10k; R0805
R2.1, R2.2, R2.3, R2.4, R2.5, R2.6: 1k; R0805
R3.1, R3.2: 47; R0805
R4.1, R4.2: 3k; R0805
R5.1, R5.2, R5.3, R5.4, R5.5, R5.6, R5.7, R5.8, R5.9, R5.10: 100k; R0805
R6.1: 1M; R0805
R7.1, R7.2, R7.3: 4k7; R0805
R8.1: 20m; R0805
SEG1.1: 7-SEGMENT-6DIGIT-FJ3661BH; 7SEG_6D_FJ3661BH
SW1.1: DHT-4235A; SW4-SMD-4.2X3.2X2.5MM
X1.1: JST-XH-06-PIN-ANGLED; JST-XH-06-PACKAGE-ROUND-PAD-ANGLED
X2.1: ZX62-B-5PA
X3.1: 61400416021

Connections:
!EN_PB: D1.2.1 (A1), IC1.25 (PC2(ADC2,PCINT10))
+5V: C1.5.2, C1.8.1, D1.3.1 (A1), IC2.1.8 (VCC), IC4.1.5 (VIN), IC5.1.5 (VS), IC6.1.16 (VDD), Q1.1.6 (D), R5.3.1, R5.5.2, R5.6.2, R7.2.2, R7.3.2
BAT_PWR: C1.1.2, C1.2.2, C2.1.2, C3.1.+, IC1.4 (VCC), IC1.18 (AVCC), R3.2.1, R5.7.1, X1.1.5
BTN_LED: IC1.8 (PB7(PCINT7)), R2.1.2, R2.5.2
BUT_MAN: IC1.2 (PD4(T0,PCINT20)), IC3.1.13 (TPQ3)
BUT_MIN: IC1.1 (PD3(INT1,PCINT19)), IC3.1.14 (TPQ2)
BUT_PLUS: IC1.31 (PD1(PCINT17)), IC3.1.16 (TPQ0)
BUT_SET: IC1.32 (PD2(INT0,PCINT18)), IC3.1.15 (TPQ1)
DIG1: IC6.1.15 (GRID1), SEG1.1.P22 (DIG1)
DIG2: IC6.1.14 (GRID2), SEG1.1.P3 (DIG2)
DIG3: IC6.1.13 (GRID3), SEG1.1.P4 (DIG3)
DIG4: IC6.1.12 (GRID4), SEG1.1.P16 (DIG4)
DIG5: IC6.1.11 (GRID5), SEG1.1.P13 (DIG5)
DIG6: IC6.1.10 (GRID6), SEG1.1.P12 (DIG6)
EN_CLK: C1.7.1, IC1.13 (PB1(OC1A,PCINT1))
EN_LOAD: IC1.30 (PD0(PCINT16)), Q2.1.2 (B), R2.4.1
GND: C1.1.1, C1.3.1, C1.4.2, C1.5.1, C1.6.1, C1.8.2, C2.1.1, C2.2.2, C2.3.2, C2.4.2, C3.1.-, C4.1.-, C5.1.2, C5.2.2, C5.3.2, C5.4.2, IC1.5 (GND), IC1.21 (GND), IC2.1.4 (GND), IC2.1.5 (A2), IC2.1.6 (A1), IC2.1.7 (A0), IC3.1.5 (AHLB), IC3.1.8 (LPMB), IC3.1.10 (VSS), IC4.1.2 (GND), IC5.1.2 (GND), IC5.1.4 (IN-), IC6.1.1 (GND), IC8.1.2 (GND), LED1.1.C, LED2.1.C, LED3.1.C, LED3.2.C, R2.6.1, R3.1.1, R5.2.2, R5.4.2, R5.8.2, R5.9.2, R6.1.2, R7.1.2, R8.1.2, SW1.1.3 (B0), X1.1.1, X2.1.5 (GND), X2.1.P1 (SHIELD), X2.1.P2 (SHIELD), X2.1.P3 (SHIELD), X2.1.P4 (SHIELD), X2.1.P5 (SHIELD), X2.1.P6 (SHIELD), X3.1.S1 (SHIELD), X3.1.S2 (SHIELD)
LED1: IC1.14 (PB2(/SS,OC1B,PCINT2)), R4.1.2
LED2: IC1.11 (PD7(AIN1,PCINT23)), R4.2.2
MISO: IC1.16 (PB4(MISO,PCINT4)), X1.1.6
MOSI: IC1.15 (PB3(MOSI,PCINT3)), X1.1.3
unnamed: IC6.1.18 (CLK), R2.2.2
unnamed: C2.3.1, IC4.1.1 (VOUT), IC8.1.5 (VIN), L1.1.1
unnamed: Q1.1.2 (S), Q1.1.5 (S)
unnamed: IC6.1.17 (DIO), R2.3.2
unnamed: D1.3.3 (C1A2), R3.2.2
unnamed: Q2.1.1 (E), Q2.2.6 (C), R3.1.2
unnamed: LED1.1.A, R4.1.1
unnamed: IC1.19 (PA0(ADC6,PCINT24)), R5.3.2, R5.4.1
unnamed: C1.7.2, D1.2.3 (C1A2)
unnamed: Q2.1.4 (E), R2.4.2
unnamed: LED2.1.A, R4.2.1
unnamed: D1.1.2 (C2), Q2.1.5 (B), Q2.1.6 (C)
unnamed: C2.2.1, R1.2.1, R1.3.2
unnamed: D1.1.1 (A1), Q2.2.1 (E), R5.1.1
unnamed: Q2.1.3 (C), Q2.2.2 (B), R5.1.2
unnamed: LED3.1.A, R2.1.1
unnamed: C1.6.2, D1.2.2 (C2), Q1.1.1 (G), Q1.1.3 (G), R6.1.1
unnamed: LED3.2.A, R2.5.1
unnamed: C2.4.1, C4.1.+, D2.1.C, R1.1.2, R5.10.2, X3.1.1 (VBUS)
unnamed: IC5.1.3 (IN+), R8.1.1, X3.1.4 (GND)
unnamed: IC4.1.3 (SET), R7.1.1
unnamed: D2.1.A, IC8.1.1 (SW), L1.1.2
unnamed: IC8.1.3 (FB), R1.1.1, R1.3.1, R2.6.2, R5.10.1
PAD_MAN: C5.4.1, IC3.1.4 (TP3)
PAD_MIN: C5.3.1, IC3.1.3 (TP2)
PAD_PLUS: C5.1.1, IC3.1.1 (TP0)
PAD_SET: C5.2.1, IC3.1.2 (TP1)
PUMP: IC1.22 (PA1(ADC7,PCINT25)), IC4.1.4 (EN), IC8.1.4 (EN), R5.2.1
PUMP_CURRENT: IC1.26 (PC3(ADC3,PCINT11)), IC5.1.1 (VOUT)
PUMP_VOL: IC1.23 (PC0(ADC0,PCINT8)), R1.2.2
RESET: C1.2.1, C1.3.2, IC1.29 (PC6(/RESET,PCINT14)), R5.7.2, SW1.1.1 (A0), X1.1.2
SCK: IC1.17 (PB5(SCK7,PCINT5)), X1.1.4
SCL: IC1.28 (PC5(ADC5,SCL,PCINT13)), IC2.1.2 (SCL), R7.3.1
SDA: IC1.27 (PC4(ADC4,SDA,PCINT12)), IC2.1.1 (SDA), R7.2.1
SEG1: IC6.1.2 (SEG1/KS1), SEG1.1.P15 (A)
SEG2: IC6.1.3 (SEG2/KS2), SEG1.1.P20 (B)
SEG3: IC6.1.4 (SEG3/KS3), SEG1.1.P19 (C)
SEG4: IC6.1.5 (SEG4/KS4), SEG1.1.P5 (D)
SEG5: IC6.1.6 (SEG5/KS5), SEG1.1.P1 (E)
SEG6: IC6.1.7 (SEG6/KS6), SEG1.1.P14 (F)
SEG7: IC6.1.8 (SEG7/KS7), SEG1.1.P17 (G)
SEG8: IC6.1.9 (SEG8/KS8), SEG1.1.P8 (DP)
TM_CLK: IC1.10 (PD6(AIN0,PCINT22)), R2.2.1, R5.5.1
TM_DIO: IC1.9 (PD5(T1,PCINT21)), R2.3.1, R5.6.1
TOUCH_PWR: C1.4.1, IC1.3 (PA2(PCINT26)), IC3.1.6 (VDD), IC3.1.11 (OD)
USB1: IC1.24 (PC1(ADC1,PCINT9)), R5.9.1, X3.1.2 (D-)
USB2: IC1.12 (PB0(CLKO,ICP1,PCINT0)), R5.8.1, X3.1.3 (D+)
VBUS: D1.1.3 (C1A2), Q1.1.4 (D), X2.1.1 (VBUS)

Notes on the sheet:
V1.4.2: - change BC847 Package - replace Jumper with Analog Switch - Use Pin13 for EN_CLK - 3k LED Resistor, leave LED on Timer Pin - red LED 3528 for Error Signal - 2 white LEDs 0805 for button light - replace female USB
normally on
Input: 5V if enabled, 2..5V if disabled
Vg_th_max < 1V
Supercap R_in=75Ohm I_max = (5V/75Ohm) = 66mA R = ?
Rin >10M
!EN_PB>2.7V -> Vg > 2*2.7-2*0.5=4.4V -> Vgs < 5V-4.4V = 0.6V !EN_PB=0V -> Vg < 0.5V after x seconds -> Vgs > -1.5V with Vs=2V
Anker big: -2.5V disabled
Blocks -2.5V if PB disabled Needs Vg < -4.5V to open
5.1V
Current Limit 1.45A
FB Voltage: 0.6V Desired Voltage: 5..6V at 0% PWM: 6.33V at 100% PWM: 4.83V
0.1*1A = 100mV P = 0.1W

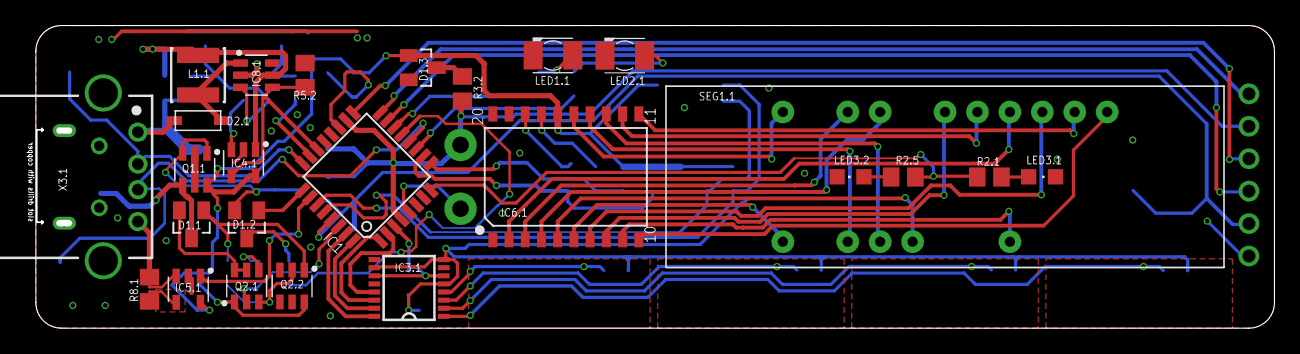
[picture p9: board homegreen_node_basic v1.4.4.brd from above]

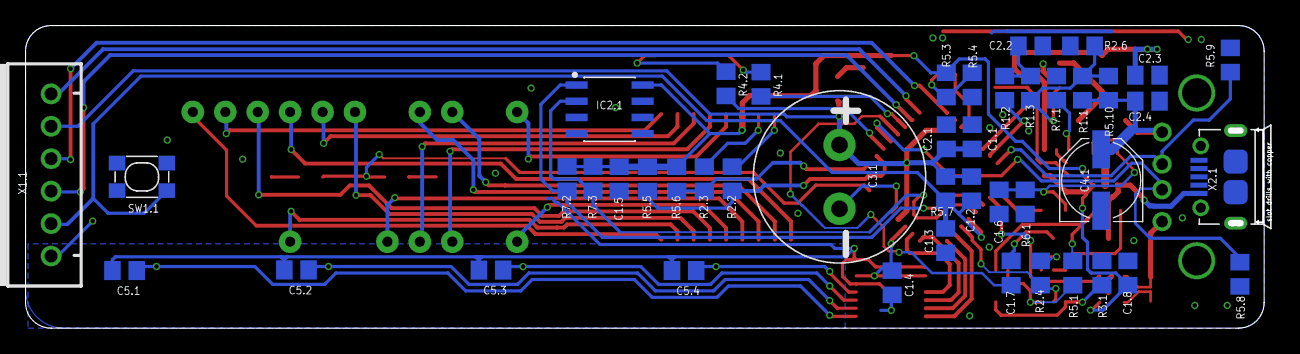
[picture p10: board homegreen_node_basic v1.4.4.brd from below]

Board: 2 copper layers, 97.0 x 23.7 mm, 70 parts (45 on the bottom side), 69 nets.

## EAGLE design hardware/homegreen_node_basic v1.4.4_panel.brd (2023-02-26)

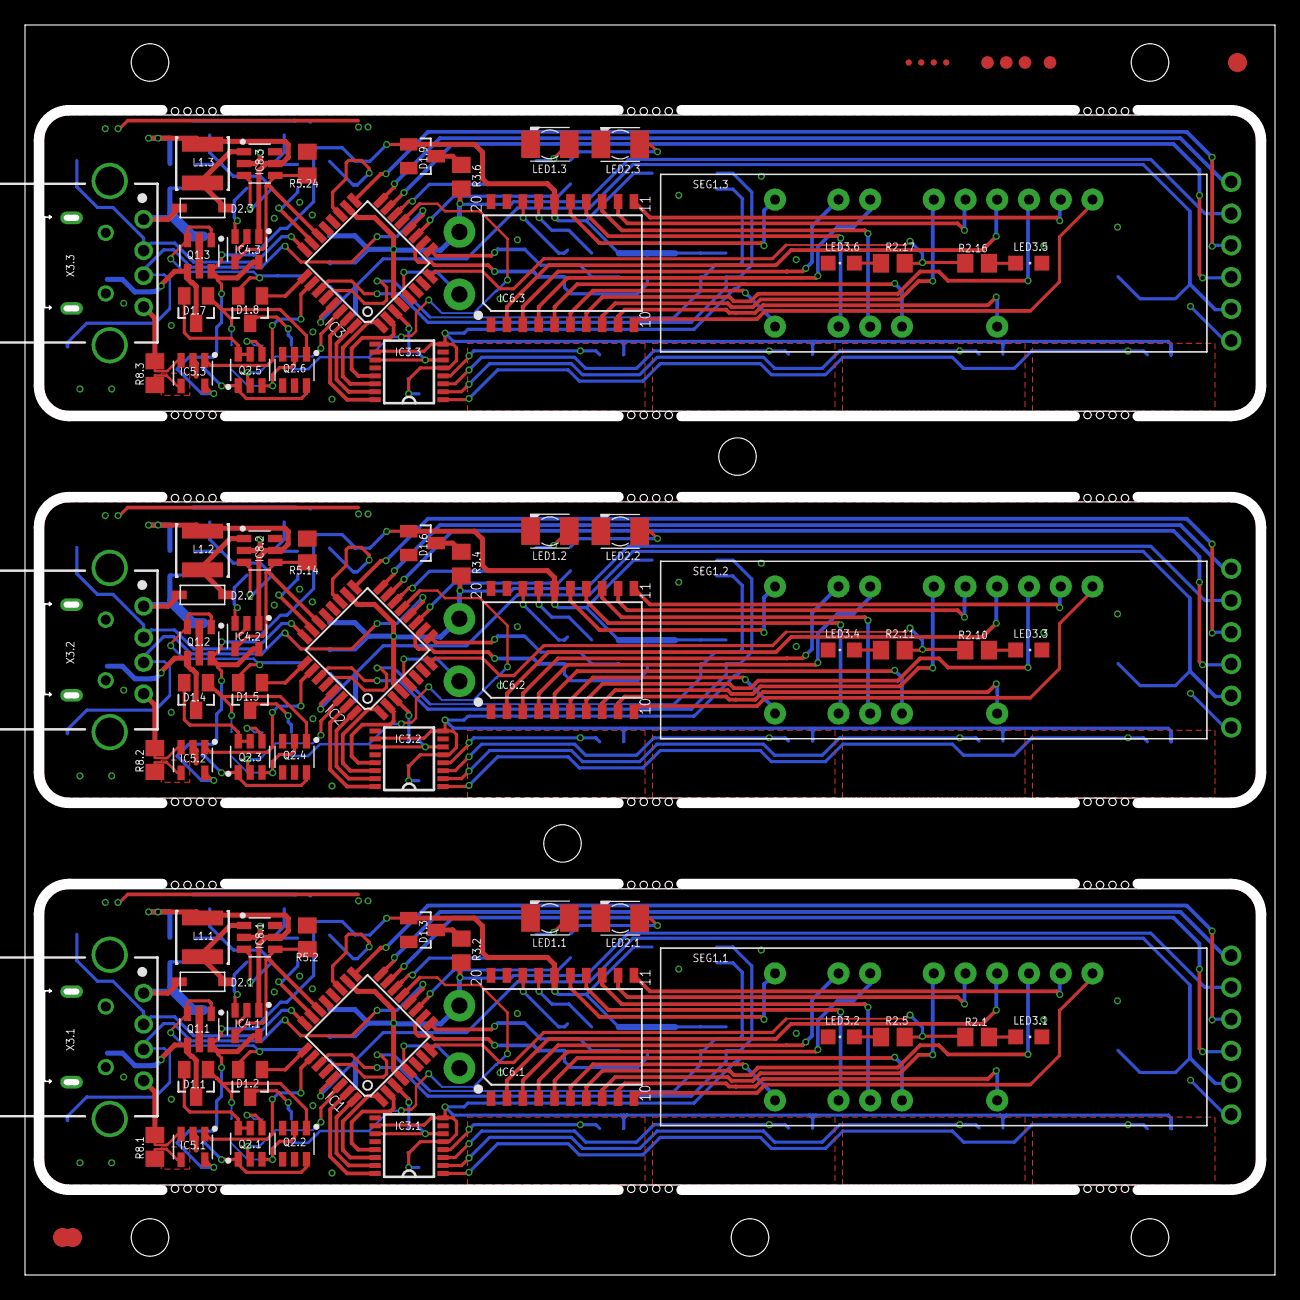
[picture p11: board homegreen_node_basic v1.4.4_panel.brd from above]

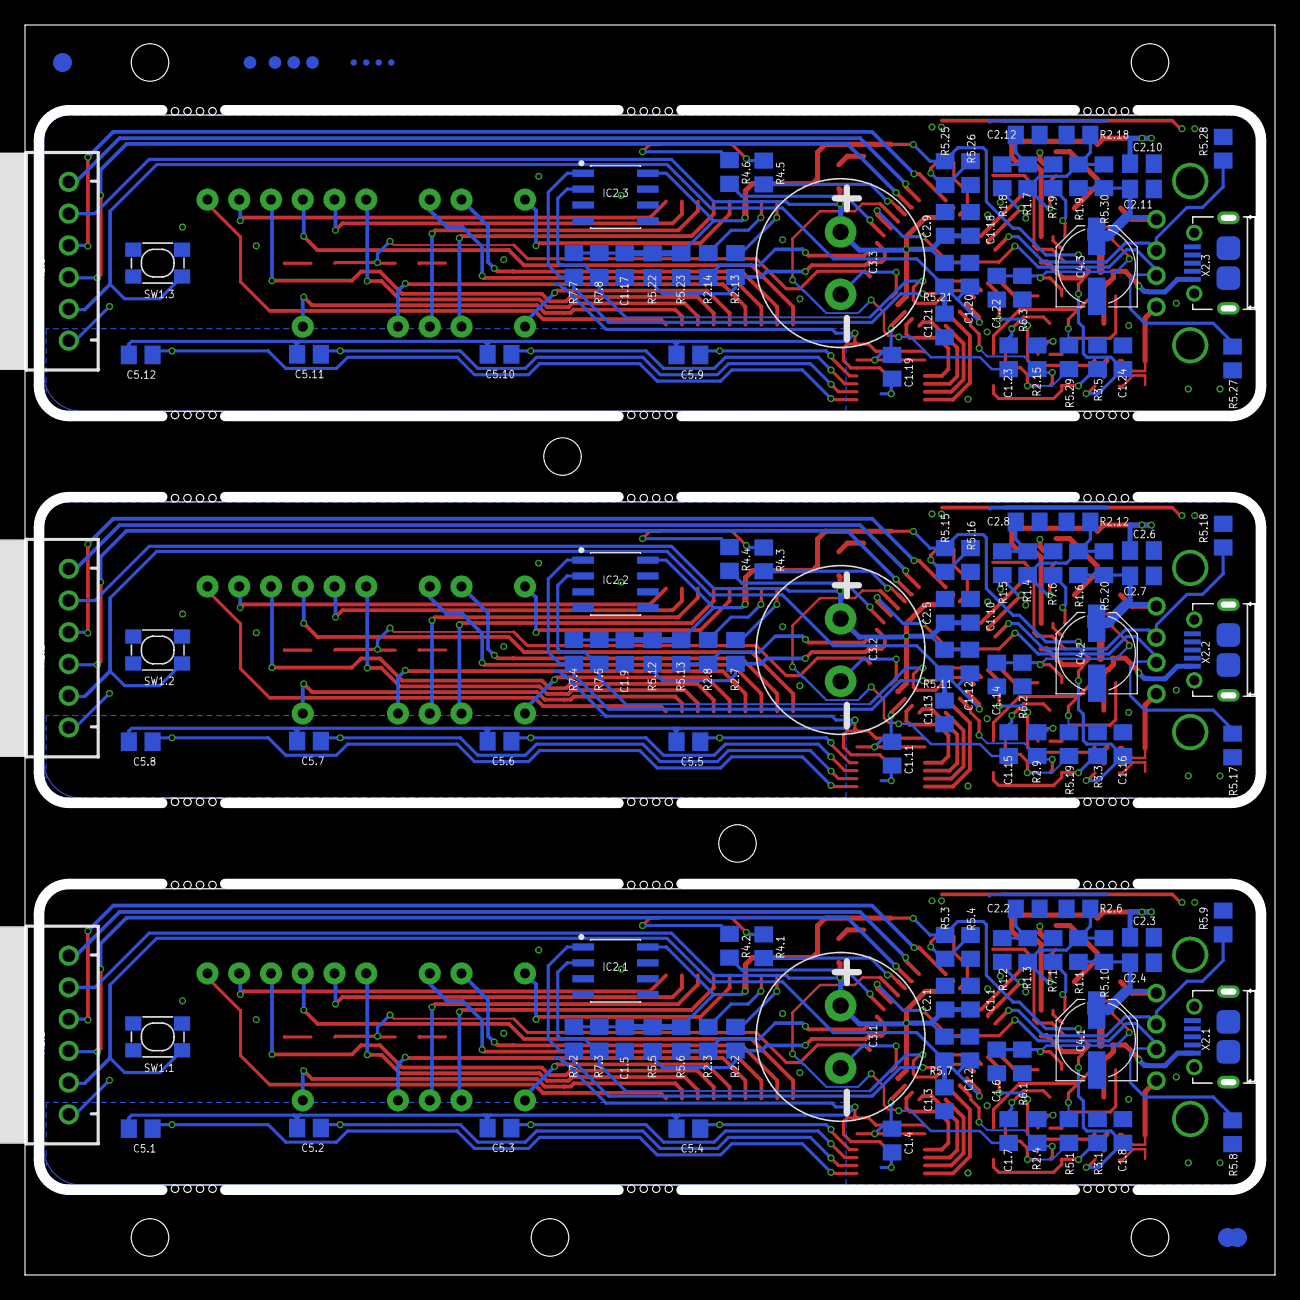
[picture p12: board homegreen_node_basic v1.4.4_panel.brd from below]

Board: 2 copper layers, 100.0 x 100.0 mm, 221 parts (135 on the bottom side), 207 nets.

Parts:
C1.1, C1.2, C1.3, C1.4, C1.5, C1.6, C1.7, C1.8, C1.9, C1.10, C1.11, C1.12, C1.13, C1.14, C1.15, C1.16, C1.17, C1.18, C1.19, C1.20, C1.21, C1.22, C1.23, C1.24: 100n; C0805
C2.1, C2.2, C2.3, C2.4, C2.5, C2.6, C2.7, C2.8, C2.9, C2.10, C2.11, C2.12: 10u; C0805
C3.1, C3.2, C3.3: 0.33F; C_FYD0H104ZF
C4.1, C4.2, C4.3: 330u; PANASONIC_D
C5.1, C5.2, C5.3, C5.4, C5.5, C5.6, C5.7, C5.8, C5.9, C5.10, C5.11, C5.12: 5p; C0805
D1.1, D1.2, D1.3, D1.4, D1.5, D1.6, D1.7, D1.8, D1.9: BAT54S; SOT23
D2.1, D2.2, D2.3: DSS24; SOD-123
E$1, E$2, E$3: FID_060_P
E$4, E$5, E$6, E$7: FID_040_P
E$8, E$9, E$10, E$11: FID_020_P
IC1, IC2, IC3: TQFP32-08
IC2.1, IC2.2, IC2.3: LM75B; SO8
IC3.1, IC3.2, IC3.3: TTP224NS; SSOP16
IC4.1, IC4.2, IC4.3: MT9700MT9700; SOT23-5
IC5.1, IC5.2, IC5.3: INA180; SOT23-5
IC6.1, IC6.2, IC6.3: TM1637-sop20; SOP20-1.27-12.7X7.65MM
IC8.1, IC8.2, IC8.3: MT3608; SOT23-6
L1.1, L1.2, L1.3: TYA40202R2M-10; WE-LQSH_4020
LED1.1, LED1.2, LED1.3: green; KA-3528ASYC
LED2.1, LED2.2, LED2.3: red; KA-3528ASYC
LED3.1, LED3.2, LED3.3, LED3.4, LED3.5, LED3.6: white; CHIPLED_0805
Q1.1, Q1.2, Q1.3: WST2011; SOT23-6
Q2.1, Q2.2, Q2.3, Q2.4, Q2.5, Q2.6: BC817DPN; SOT23-6
R1.1, R1.2, R1.3, R1.4, R1.5, R1.6, R1.7, R1.8, R1.9: 10k; R0805
R2.1, R2.2, R2.3, R2.4, R2.5, R2.6, R2.7, R2.8, R2.9, R2.10, R2.11, R2.12, R2.13, R2.14, R2.15, R2.16, R2.17, R2.18: 1k; R0805
R3.1, R3.2, R3.3, R3.4, R3.5, R3.6: 47; R0805
R4.1, R4.2, R4.3, R4.4, R4.5, R4.6: 3k; R0805
R5.1, R5.2, R5.3, R5.4, R5.5, R5.6, R5.7, R5.8, R5.9, R5.10, R5.11, R5.12, R5.13, R5.14, R5.15, R5.16, R5.17, R5.18, R5.19, R5.20, R5.21, R5.22, R5.23, R5.24, R5.25, R5.26, R5.27, R5.28, R5.29, R5.30: 100k; R0805
R6.1, R6.2, R6.3: 1M; R0805
R7.1, R7.2, R7.3, R7.4, R7.5, R7.6, R7.7, R7.8, R7.9: 4k7; R0805
R8.1, R8.2, R8.3: 20m; R0805
SEG1.1, SEG1.2, SEG1.3: 7-SEGMENT-6DIGIT-FJ3661BH; 7SEG_6D_FJ3661BH
SW1.1, SW1.2, SW1.3: DHT-4235A; SW4-SMD-4.2X3.2X2.5MM
X1.1, X1.2, X1.3: JST-XH-06-PIN-ANGLED; JST-XH-06-PACKAGE-ROUND-PAD-ANGLED
X2.1, X2.2, X2.3: ZX62-B-5PA
X3.1, X3.2, X3.3: 61400416021

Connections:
!EN_PB: D1.2.1, IC1.25
!EN_PB1: D1.5.1, IC2.25
!EN_PB2: D1.8.1, IC3.25
+5V: C1.5.2, C1.8.1, D1.3.1, IC2.1.8, IC4.1.5, IC5.1.5, IC6.1.16, Q1.1.6, R5.3.1, R5.5.2, R5.6.2, R7.2.2, R7.3.2
+5V1: C1.9.2, C1.16.1, D1.6.1, IC2.2.8, IC4.2.5, IC5.2.5, IC6.2.16, Q1.2.6, R5.12.2, R5.13.2, R5.15.1, R7.4.2, R7.5.2
+5V2: C1.17.2, C1.24.1, D1.9.1, IC2.3.8, IC4.3.5, IC5.3.5, IC6.3.16, Q1.3.6, R5.22.2, R5.23.2, R5.25.1, R7.7.2, R7.8.2
BAT_PWR: C1.1.2, C1.2.2, C2.1.2, C3.1.+, IC1.4, IC1.18, R3.2.1, R5.7.1, X1.1.5
BAT_PWR1: C1.10.2, C1.12.2, C2.5.2, C3.2.+, IC2.4, IC2.18, R3.4.1, R5.11.1, X1.2.5
BAT_PWR2: C1.18.2, C1.20.2, C2.9.2, C3.3.+, IC3.4, IC3.18, R3.6.1, R5.21.1, X1.3.5
BTN_LED: IC1.8, R2.1.2, R2.5.2
BTN_LED1: IC2.8, R2.10.2, R2.11.2
BTN_LED2: IC3.8, R2.16.2, R2.17.2
BUT_MAN: IC1.2, IC3.1.13
BUT_MAN1: IC2.2, IC3.2.13
BUT_MAN2: IC3.2, IC3.3.13
BUT_MIN: IC1.1, IC3.1.14
BUT_MIN1: IC2.1, IC3.2.14
BUT_MIN2: IC3.1, IC3.3.14
BUT_PLUS: IC1.31, IC3.1.16
BUT_PLUS1: IC2.31, IC3.2.16
BUT_PLUS2: IC3.31, IC3.3.16
BUT_SET: IC1.32, IC3.1.15
BUT_SET1: IC2.32, IC3.2.15
BUT_SET2: IC3.32, IC3.3.15
DIG1: IC6.1.15, SEG1.1.P22
DIG2: IC6.1.14, SEG1.1.P3
DIG3: IC6.1.13, SEG1.1.P4
DIG4: IC6.1.12, SEG1.1.P16
DIG5: IC6.1.11, SEG1.1.P13
DIG6: IC6.1.10, SEG1.1.P12
DIG7: IC6.2.10, SEG1.2.P12
DIG8: IC6.2.11, SEG1.2.P13
DIG9: IC6.2.12, SEG1.2.P16
DIG10: IC6.2.13, SEG1.2.P4
DIG11: IC6.2.14, SEG1.2.P3
DIG12: IC6.2.15, SEG1.2.P22
DIG13: IC6.3.10, SEG1.3.P12
DIG14: IC6.3.11, SEG1.3.P13
DIG15: IC6.3.12, SEG1.3.P16
DIG16: IC6.3.13, SEG1.3.P4
DIG17: IC6.3.14, SEG1.3.P3
DIG18: IC6.3.15, SEG1.3.P22
EN_CLK: C1.7.1, IC1.13
EN_CLK1: C1.15.1, IC2.13
EN_CLK2: C1.23.1, IC3.13
EN_LOAD: IC1.30, Q2.1.2, R2.4.1
EN_LOAD1: IC2.30, Q2.3.2, R2.9.1
EN_LOAD2: IC3.30, Q2.5.2, R2.15.1
GND: C1.1.1, C1.3.1, C1.4.2, C1.5.1, C1.6.1, C1.8.2, C2.1.1, C2.2.2, C2.3.2, C2.4.2, C3.1.-, C4.1.-, C5.1.2, C5.2.2, C5.3.2, C5.4.2, IC1.5, IC1.21, IC2.1.4, IC2.1.5, IC2.1.6, IC2.1.7, IC3.1.5, IC3.1.8, IC3.1.10, IC4.1.2, IC5.1.2, IC5.1.4, IC6.1.1, IC8.1.2, LED1.1.C, LED2.1.C, LED3.1.C, LED3.2.C, R2.6.1, R3.1.1, R5.2.2, R5.4.2, R5.8.2, R5.9.2, R6.1.2, R7.1.2, R8.1.2, SW1.1.3, X1.1.1, X2.1.5, X2.1.P1, X2.1.P2, X2.1.P3, X2.1.P4, X2.1.P5, X2.1.P6, X3.1.S1, X3.1.S2
GND1: C1.9.1, C1.10.1, C1.11.2, C1.13.1, C1.14.1, C1.16.2, C2.5.1, C2.6.2, C2.7.2, C2.8.2, C3.2.-, C4.2.-, C5.5.2, C5.6.2, C5.7.2, C5.8.2, IC2.5, IC2.21, IC2.2.4, IC2.2.5, IC2.2.6, IC2.2.7, IC3.2.5, IC3.2.8, IC3.2.10, IC4.2.2, IC5.2.2, IC5.2.4, IC6.2.1, IC8.2.2, LED1.2.C, LED2.2.C, LED3.3.C, LED3.4.C, R2.12.1, R3.3.1, R5.14.2, R5.16.2, R5.17.2, R5.18.2, R6.2.2, R7.6.2, R8.2.2, SW1.2.3, X1.2.1, X2.2.5, X2.2.P1, X2.2.P2, X2.2.P3, X2.2.P4, X2.2.P5, X2.2.P6, X3.2.S1, X3.2.S2
GND4: C1.17.1, C1.18.1, C1.19.2, C1.21.1, C1.22.1, C1.24.2, C2.9.1, C2.10.2, C2.11.2, C2.12.2, C3.3.-, C4.3.-, C5.9.2, C5.10.2, C5.11.2, C5.12.2, IC2.3.4, IC2.3.5, IC2.3.6, IC2.3.7, IC3.5, IC3.21, IC3.3.5, IC3.3.8, IC3.3.10, IC4.3.2, IC5.3.2, IC5.3.4, IC6.3.1, IC8.3.2, LED1.3.C, LED2.3.C, LED3.5.C, LED3.6.C, R2.18.1, R3.5.1, R5.24.2, R5.26.2, R5.27.2, R5.28.2, R6.3.2, R7.9.2, R8.3.2, SW1.3.3, X1.3.1, X2.3.5, X2.3.P1, X2.3.P2, X2.3.P3, X2.3.P4, X2.3.P5, X2.3.P6, X3.3.S1, X3.3.S2
LED1: IC1.14, R4.1.2
LED2: IC1.11, R4.2.2
LED3: IC2.11, R4.4.2
LED4: IC2.14, R4.3.2
LED5: IC3.11, R4.6.2
LED6: IC3.14, R4.5.2
MISO: IC1.16, X1.1.6
MISO1: IC2.16, X1.2.6
MISO2: IC3.16, X1.3.6
MOSI: IC1.15, X1.1.3
MOSI1: IC2.15, X1.2.3
MOSI2: IC3.15, X1.3.3
unnamed: IC6.1.18, R2.2.2
unnamed: C2.3.1, IC4.1.1, IC8.1.5, L1.1.1
unnamed: Q1.1.2, Q1.1.5
unnamed: IC6.1.17, R2.3.2
unnamed: D1.3.3, R3.2.2
unnamed: Q2.1.1, Q2.2.6, R3.1.2
unnamed: LED1.1.A, R4.1.1
unnamed: IC1.19, R5.3.2, R5.4.1
unnamed: C1.7.2, D1.2.3
unnamed: Q2.1.4, R2.4.2
unnamed: LED2.1.A, R4.2.1
unnamed: D1.1.2, Q2.1.5, Q2.1.6
unnamed: C2.2.1, R1.2.1, R1.3.2
unnamed: D1.1.1, Q2.2.1, R5.1.1
unnamed: Q2.1.3, Q2.2.2, R5.1.2
unnamed: LED3.1.A, R2.1.1
unnamed: C1.6.2, D1.2.2, Q1.1.1, Q1.1.3, R6.1.1
unnamed: LED3.2.A, R2.5.1
unnamed: C2.4.1, C4.1.+, D2.1.C, R1.1.2, R5.10.2, X3.1.1
unnamed: D1.6.3, R3.4.2
unnamed: LED1.2.A, R4.3.1
unnamed: IC5.1.3, R8.1.1, X3.1.4
unnamed: IC4.1.3, R7.1.1
unnamed: IC6.2.18, R2.7.2
unnamed: IC6.2.17, R2.8.2
unnamed: IC2.19, R5.15.2, R5.16.1
unnamed: C1.14.2, D1.5.2, Q1.2.1, Q1.2.3, R6.2.1
unnamed: Q2.3.1, Q2.4.6, R3.3.2
unnamed: D1.4.2, Q2.3.5, Q2.3.6
unnamed: D2.1.A, IC8.1.1, L1.1.2
unnamed: IC8.1.3, R1.1.1, R1.3.1, R2.6.2, R5.10.1
unnamed: D1.4.1, Q2.4.1, R5.19.1
unnamed: Q2.3.3, Q2.4.2, R5.19.2
unnamed: Q2.3.4, R2.9.2
unnamed: Q1.2.2, Q1.2.5
unnamed: C1.15.2, D1.5.3
unnamed: LED2.2.A, R4.4.1
unnamed: LED3.3.A, R2.10.1
unnamed: LED3.4.A, R2.11.1
unnamed: D2.2.A, IC8.2.1, L1.2.2
unnamed: IC8.2.3, R1.4.1, R1.6.1, R2.12.2, R5.20.1
unnamed: C2.7.1, C4.2.+, D2.2.C, R1.6.2, R5.20.2, X3.2.1
unnamed: C2.8.1, R1.4.2, R1.5.1
unnamed: C2.6.1, IC4.2.1, IC8.2.5, L1.2.1
unnamed: IC4.2.3, R7.6.1
unnamed: IC5.2.3, R8.2.1, X3.2.4
unnamed: D1.9.3, R3.6.2
unnamed: LED1.3.A, R4.5.1
unnamed: IC6.3.18, R2.13.2
unnamed: IC6.3.17, R2.14.2
unnamed: IC3.19, R5.25.2, R5.26.1
unnamed: C1.22.2, D1.8.2, Q1.3.1, Q1.3.3, R6.3.1
unnamed: Q2.5.1, Q2.6.6, R3.5.2
unnamed: D1.7.2, Q2.5.5, Q2.5.6
unnamed: D1.7.1, Q2.6.1, R5.29.1
unnamed: Q2.5.3, Q2.6.2, R5.29.2
unnamed: Q2.5.4, R2.15.2
unnamed: Q1.3.2, Q1.3.5
unnamed: C1.23.2, D1.8.3
unnamed: LED2.3.A, R4.6.1
unnamed: LED3.5.A, R2.16.1
unnamed: LED3.6.A, R2.17.1
unnamed: D2.3.A, IC8.3.1, L1.3.2
unnamed: IC8.3.3, R1.7.1, R1.9.1, R2.18.2, R5.30.1
unnamed: C2.11.1, C4.3.+, D2.3.C, R1.9.2, R5.30.2, X3.3.1
unnamed: C2.12.1, R1.7.2, R1.8.1
unnamed: C2.10.1, IC4.3.1, IC8.3.5, L1.3.1
unnamed: IC4.3.3, R7.9.1
unnamed: IC5.3.3, R8.3.1, X3.3.4
PAD_MAN: C5.4.1, IC3.1.4
PAD_MAN1: C5.5.1, IC3.2.4
PAD_MAN2: C5.9.1, IC3.3.4
PAD_MIN: C5.3.1, IC3.1.3
PAD_MIN1: C5.6.1, IC3.2.3
PAD_MIN2: C5.10.1, IC3.3.3
PAD_PLUS: C5.1.1, IC3.1.1
PAD_PLUS1: C5.8.1, IC3.2.1
PAD_PLUS2: C5.12.1, IC3.3.1
PAD_SET: C5.2.1, IC3.1.2
PAD_SET1: C5.7.1, IC3.2.2
PAD_SET2: C5.11.1, IC3.3.2
PUMP: IC1.22, IC4.1.4, IC8.1.4, R5.2.1
PUMP1: IC2.22, IC4.2.4, IC8.2.4, R5.14.1
PUMP2: IC3.22, IC4.3.4, IC8.3.4, R5.24.1
PUMP_CURRENT: IC1.26, IC5.1.1
PUMP_CURRENT1: IC2.26, IC5.2.1
PUMP_CURRENT2: IC3.26, IC5.3.1
PUMP_VOL: IC1.23, R1.2.2
PUMP_VOL1: IC2.23, R1.5.2
PUMP_VOL2: IC3.23, R1.8.2
RESET: C1.2.1, C1.3.2, IC1.29, R5.7.2, SW1.1.1, X1.1.2
RESET1: C1.12.1, C1.13.2, IC2.29, R5.11.2, SW1.2.1, X1.2.2
RESET2: C1.20.1, C1.21.2, IC3.29, R5.21.2, SW1.3.1, X1.3.2
SCK: IC1.17, X1.1.4
SCK1: IC2.17, X1.2.4
SCK2: IC3.17, X1.3.4
SCL: IC1.28, IC2.1.2, R7.3.1
SCL1: IC2.28, IC2.2.2, R7.5.1
SCL2: IC2.3.2, IC3.28, R7.8.1
SDA: IC1.27, IC2.1.1, R7.2.1
SDA1: IC2.27, IC2.2.1, R7.4.1
SDA2: IC2.3.1, IC3.27, R7.7.1
SEG1: IC6.1.2, SEG1.1.P15
SEG2: IC6.1.3, SEG1.1.P20
SEG3: IC6.1.4, SEG1.1.P19
SEG4: IC6.1.5, SEG1.1.P5
SEG5: IC6.1.6, SEG1.1.P1
SEG6: IC6.1.7, SEG1.1.P14
SEG7: IC6.1.8, SEG1.1.P17
SEG8: IC6.1.9, SEG1.1.P8
SEG9: IC6.2.2, SEG1.2.P15
SEG10: IC6.2.3, SEG1.2.P20
SEG11: IC6.2.4, SEG1.2.P19
SEG12: IC6.2.5, SEG1.2.P5
SEG13: IC6.2.6, SEG1.2.P1
SEG14: IC6.2.7, SEG1.2.P14
SEG15: IC6.2.8, SEG1.2.P17
SEG16: IC6.2.9, SEG1.2.P8
SEG17: IC6.3.2, SEG1.3.P15
SEG18: IC6.3.3, SEG1.3.P20
SEG19: IC6.3.4, SEG1.3.P19
SEG20: IC6.3.5, SEG1.3.P5
SEG21: IC6.3.6, SEG1.3.P1
SEG22: IC6.3.7, SEG1.3.P14
SEG23: IC6.3.8, SEG1.3.P17
SEG24: IC6.3.9, SEG1.3.P8
TM_CLK: IC1.10, R2.2.1, R5.5.1
TM_CLK1: IC2.10, R2.7.1, R5.12.1
TM_CLK2: IC3.10, R2.13.1, R5.22.1
TM_DIO: IC1.9, R2.3.1, R5.6.1
TM_DIO1: IC2.9, R2.8.1, R5.13.1
TM_DIO2: IC3.9, R2.14.1, R5.23.1
TOUCH_PWR: C1.4.1, IC1.3, IC3.1.6, IC3.1.11
TOUCH_PWR1: C1.11.1, IC2.3, IC3.2.6, IC3.2.11
TOUCH_PWR2: C1.19.1, IC3.3, IC3.3.6, IC3.3.11
USB1: IC1.24, R5.9.1, X3.1.2
USB2: IC1.12, R5.8.1, X3.1.3
USB3: IC2.24, R5.18.1, X3.2.2
USB4: IC2.12, R5.17.1, X3.2.3
USB5: IC3.24, R5.28.1, X3.3.2
USB6: IC3.12, R5.27.1, X3.3.3
VBUS: D1.1.3, Q1.1.4, X2.1.1
VBUS1: D1.4.3, Q1.2.4, X2.2.1
VBUS2: D1.7.3, Q1.3.4, X2.3.1

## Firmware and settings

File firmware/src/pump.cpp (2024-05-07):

/*
 * PUMP.c
 *
 *  Created on: 17.01.2019
 *      Author: pmale
 */

#include "pump.hpp"

DeltaTimer Pump::pumpTimer;
uint16_t Pump::pumpCounter = 0;
uint8_t Pump::currentPump = PUMP_1;

void Pump::Init()
{
	PUMP_DDR |= _BV(PUMP_PIN);					//Set Pump Pin as Output
	PUMP_PORT &= ~_BV(PUMP_PIN);				//turn off Pump Pin

#ifdef FEATURE_PUMP_STRENGTH
	PUMP_VOL_DDR |= _BV(PUMP_VOL_PIN);			//Set Pump Voltage Pin as Output
	PUMP_VOL_PORT &= ~_BV(PUMP_VOL_PIN);		//set Pump Voltage Pin low
#endif
#ifdef FEATURE_PUMP_SENSOR
	PUMP_CUR_DDR &= ~_BV(PUMP_CUR_PIN);			//pump current pin as input
#endif

	pumpCounter = 0;
	pumpTimer.setTimeStep(1000); 				//1 second
	currentPump = PUMP_1;

    USB_OUT_P_DDR |= _BV(USB_OUT_P_PIN);        //USB1 Output
    USB_OUT_M_DDR |= _BV(USB_OUT_M_PIN);        //USB2 Output
    USB_OUT_P_PORT &= ~_BV(USB_OUT_P_PIN);      //set low
    USB_OUT_M_PORT &= ~_BV(USB_OUT_M_PIN);      //set low

}

void Pump::run()
{
	switch (Data::GetPumpStrength(currentPump))
	{
	case 0:
		PUMP_VOL_PORT |= _BV(PUMP_VOL_PIN); //turn high for low strength
		break;
	case 1:
		PUMP_VOL_PORT ^= _BV(PUMP_VOL_PIN); //toggle for medium strength
		break;
	case 2:
		PUMP_VOL_PORT &= ~_BV(PUMP_VOL_PIN); //turn low for high strength
		break;
	}
	if(pumpTimer.isTimeUp()) //1000ms
	{
		if(pumpCounter > 0)	//if enabled
		{
			PUMP_PORT |= _BV(PUMP_PIN);	//turn on
			pumpCounter--;	//countdown
		}
		else
		{
			PUMP_PORT &= ~_BV(PUMP_PIN);	//turn off
		}
#ifdef FEATURE_PUMP_STRENGTH_OSCILLATING
		static uint8_t dir = 0;
		if(Data::GetPumpStrength(currentPump) == 2)
		{
			dir = 1;
		}
		else if (Data::GetPumpStrength(currentPump) == 0)
		{
			dir = 0;
		}
		Data::SetPumpStrength(currentPump,dir ? Data::GetPumpStrength(currentPump)-1 : Data::GetPumpStrength(currentPump)+1);
#endif
	}
}

void Pump::Start()
{
	currentPump = PUMP_1;
	Data::SetPumpStrength(currentPump,0);
	pumpTimer.reset();
}

void Pump::setCountdown(uint16_t sec)
{
	pumpCounter = sec;
}

void Pump::Increment()	//1min steps
{
	pumpCounter += 60;
}

void Pump::Decrement()	//1min steps
{
	if(pumpCounter >60)
	{
		pumpCounter -= 60;
	}
}

void Pump::Stop()
{
	pumpCounter = 0;
	PUMP_PORT &= ~_BV(PUMP_PIN);	//turn off
}

uint16_t Pump::getCountdown()
{
	return pumpCounter;
}

uint8_t Pump::getCurrentPump()
{
	return currentPump;
}

bool Pump::isHubConnected()
{
	uint8_t usb1_cnt = 0, usb2_cnt = 0;

	PUMP_PORT |= _BV(PUMP_PIN);	//turn on

    USB_OUT_P_DDR &= ~_BV(USB_OUT_P_PIN);                //USBP Input
    USB_OUT_M_DDR &= ~_BV(USB_OUT_M_PIN);                //USB2 Input
    USB_OUT_P_PORT &= ~_BV(USB_OUT_P_PIN);                    //No PullUp
    USB_OUT_M_PORT &= ~_BV(USB_OUT_M_PIN);                    //No PullUp
    _delay_ms(10);

    for(uint8_t i=0;i<10;i++)    //check pin 10 times to ignore floating pin
    {
		if(USB_OUT_P_PINREG & _BV(USB_OUT_P_PIN))
		{
			usb1_cnt++;
		}
		if(USB_OUT_M_PINREG & _BV(USB_OUT_M_PIN))
		{
			usb2_cnt++;
		}
        _delay_ms(1);
    }
	PUMP_PORT &= ~_BV(PUMP_PIN);	//turn off
    USB_OUT_P_DDR |= _BV(USB_OUT_P_PIN);                //USBP Output
    USB_OUT_M_DDR |= _BV(USB_OUT_M_PIN);                //USB2 Output
    USB_OUT_P_PORT &= ~_BV(USB_OUT_P_PIN);                //set low
    USB_OUT_M_PORT &= ~_BV(USB_OUT_M_PIN);                //set low

    if(usb1_cnt > 8 && usb2_cnt < 2)    //Hub Detection, High on USB+, Low on USB-
    {
        return true;
    }
    else
    {
        return false;
    }
}

void Pump::setCurrentPump(uint8_t pumpID)
{
	switch (pumpID) {
		case PUMP_1:
			currentPump = PUMP_1;
		    USB_OUT_P_PORT &= ~_BV(USB_OUT_P_PIN);                //0 0 -> pump 1
		    USB_OUT_M_PORT &= ~_BV(USB_OUT_M_PIN);
			break;
		case PUMP_2:
			currentPump = PUMP_2;
		    USB_OUT_P_PORT |= _BV(USB_OUT_P_PIN);                //1 1 -> pump 2
		    USB_OUT_M_PORT |= _BV(USB_OUT_M_PIN);
			break;
		case PUMP_3:
			currentPump = PUMP_3;
		    USB_OUT_P_PORT &= ~_BV(USB_OUT_P_PIN);                //0 1 -> pump 3
		    USB_OUT_M_PORT |= _BV(USB_OUT_M_PIN);
			break;
	}
}

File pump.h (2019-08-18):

/*
 * PUMP.h
 *
 *  Created on: 17.01.2019
 *      Author: pmale
 */

#ifndef PUMP_H_
#define PUMP_H_

#define PUMP_DDR DDRA
#define PUMP_PORT PORTA
#define PUMP_PIN PA1

#define PUMP_SIG_DDR DDRA
#define PUMP_SIG_PORT PORTA
#define PUMP_SIG_PIN PA0

#define PUMP_TEST_DDR DDRC
#define PUMP_TEST_PORT PORTC
#define PUMP_TEST_PIN PC7

void pump_init();

void pump_vSyncTask();	//10ms

void pump_enable(uint16_t val);

void pump_disable();

uint16_t pump_getCountdown();

void pump_setPower(uint8_t pow);

uint8_t pump_getPower();


#endif /* PUMP_H_ */

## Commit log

2019-03-31 uploading current state
2019-03-31 adapted pin names
2019-04-01 port of Pin definitions done, compiles without warnings
2019-04-04 removing software based I2C Master
2019-04-10 correct button definition, + and - swapped working buzzer, but needs a diode to not destroy the pcb
    [button.h]
2019-04-10 adding current and setup temp to DATA adding duration adjustment implementation
2019-04-22 update Build number this release is on the first 4 pcbs sent to HQ
2019-04-29 adding boot animation fixing PowerInput switch from Powerbank to battery, reset pin was the issue
2019-05-19 using peter fleury i2c library
2019-06-26 moved files removed temp sensor from code, as it causes system brick
2019-06-26 fixing parasitic power of 7segment ic over data line
    [tm1637.c]
2019-06-26 implemented powerState such that it runs independently removed powerChange callback
2019-06-27 adding pump test and sig pin checking if power lost while pumping and goto sleep tweaking buzzer
    [pump.h]
2019-06-28 using Frequency Lookup Table instead of division inside interrupt routine to mitigate performance issues Adding a pump disable once power is lost while pumping
2019-06-28 changing ADC from onDemand to Free Running mode Implemented a ringBuffer to remove ADC measurement spikes
2019-06-28 adding a ADC Stable flag which signalizes if 10 measurements are completed after initialization
2019-08-17 disable heartbeat fix adc_stable
    [power.c]
2019-08-20 removed buzzer display timeout to 5s load counter to 2s
    [PLATFORM.h, power.c]
2019-09-07 Use Buzzer pin as sleep debug pin. LOW if in sleep, HIGH if active
2019-11-15 add charge cap functionality removed pump power lost feature
2020-03-08 cleanup of power
2020-03-14 buttons working, power detection still patched out
2020-03-16 fixed hello animation fixed pump counter using 5V Pin for isPowerConnected -> works great! after reset -> blink blue if no PB connected -> blink green if PB connected
    [power.cpp]
2020-03-21 Adding MAN Long Press in Config mode for resetting data. Using 5V Pin for Power detection
    [power.cpp]
2020-04-11 pull down i2c and tm pins in sleep to keep 5V low use ADC for cap measurement instead of BOD -> disable by fuses again
2020-04-12 implementing Clock Output for voltage doubler
2020-04-12 switched back to 1MHz
2020-04-23 fixing LED blink
2020-05-09 Adding Info Screen, Moving Reset to Info Screen
    [PLATFORM.h]
2020-05-10 Fixed Temp Display Fixed Blinking Added totalRuntime, saves every day Fixed HubDisplay Removed Pump Decrement below 1min
    [PLATFORM.h, pump.cpp]
2020-05-11 renamed Signal moved all Pin Definitions to PLATFORM.h
2020-05-14 Disable Brownout Remove Display Charge Animation, replacing with LED Fade replace all delays with Short Sleeps Add Solar Signal 1sec before wakeup of powerbank Increase LowVoltage to 3V Fixing Temp S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
    [Led.hpp, PLATFORM.h]
2020-05-20 - added status bits and ignore status bits to data structure - added error state to display last error - removed boot animation, directly to sleep on powerup - added separate charge state, with no UI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
    - changed button threshold to 50ms
    - code cleanup
    [Led.hpp, PLATFORM.h, button.hpp]
2020-05-20 - added ignoreFunctionality - added customCountdown Function for delayed PBTest - fixed glitchy Display Wake - added PBError Functionality - Pump Test not working on current HW, removed
    [pump.cpp]
2020-06-22 Changed Sleep Timer Source from WDT to Timer0, 250ms Timer Timer1 now responsible for both Clock Source and active 1ms Clock Included CRC Protection for EEPROM Corruption Detection Implemented EEPROM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
    [PLATFORM.h, button.hpp]
2020-09-12 applied changes for new hardware. Removed Pump Check. Added multiple LEDs
2020-09-12 fixed timer sleep not feeding watchdog disabling solar charger for now
2020-09-14 fixed runtime Timer added savePending to EEPROM to delay save to higher voltage state fixed EEPROM CRC added redgreen LED Blink
    [Led.hpp]
2022-07-06 - changed pin definitions for hw1.4.4 - added multiple environments to build multiple targets
2022-07-08 - removing temp sensor
2022-07-08 - Feature Pump Strength done
2023-02-26 cleanup and add readme
    [VOut_calc.xlsx, homegreen_node_basic v1.4.3 BOM.xlsx, homegreen_node_basic v1.4.3 order.xlsx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]
2024-04-19 - fix platformio config - add pump oscillating feature
    [PLATFORM.h, pump.cpp]
2024-04-19 update BRD and BOM
    [homegreen_node_basic v1.4.4 BOM.xlsx, homegreen_node_basic v1.4.4.brd]
2024-04-19 add kicad files
    [Homegreen Node Basic.kicad_pcb, Homegreen Node Basic.kicad_sch, power_management.kicad_sch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]
2024-05-05 - switched back to 1.8V BOD, necessary for Solar PB - increased blink Delay while sleep to 8s and charging to 4s - added charging dependency on PB Fill State - modified wake pattern - increased Cap c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
    [PLATFORM.h, power.cpp, power.hpp]
2024-05-07 - simplify wakeup code - added 2.5s delay beofre starting to pump - added pump start animation
2024-06-12 - added 5V Pin debouncing
2024-07-10 add clearing of PB Error, when the last pump cycle was successful
    [PLATFORM.h]
2025-04-19 Kicad update
    [Homegreen Node Basic.kicad_sch, power_management.kicad_sch, user_interface.kicad_sch]

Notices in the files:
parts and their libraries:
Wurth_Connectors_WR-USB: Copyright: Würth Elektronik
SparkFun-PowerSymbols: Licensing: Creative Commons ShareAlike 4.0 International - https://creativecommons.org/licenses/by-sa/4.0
